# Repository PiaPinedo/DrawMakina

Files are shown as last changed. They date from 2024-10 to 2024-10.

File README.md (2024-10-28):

# DrawMakina
Máquina de dibujo Open Source 



DrawMakina es una maquina de dibujo DIY, Open Source y de bajo coste para dibujar con hojas tamaño A2.

Fabricada con perfiles V-slot , piezas impresas en 3d y carcasa cortada con laser cnc.

En este repositorio podrás acceder a la lista de piezas, el detalle del ensamblaje y las piezas para imprimir 3d.
DM completa
## Table of Contents
- [Listado Componentes](#listado-componentes)
- [Piezas STL-Para impresión 3D](#piezas-stl-para-impresión-3d)
- [Planos Ensamblaje](#planos-ensamblaje)
  - [Planos piezas con insertos](#planos-piezas-con-insertos)
  - [Planos Carro](#planos-carro)
  - [Planos Eje X](#planos-eje-x)
  - [Planos Eje Y+Base](#planos-eje-ybase)
  - [Planos Caja Electrónica](#planos-caja-electrónica)
  - [Planos Ensamble DrawMakina](#planos-ensamble-drawmakina)
- [Instagram](#instagram)

### [Listado Componentes](https://docs.google.com/spreadsheets/d/1AmNRzkBurb7ddMvps6KCj8CBwCPvgpXAdZpDU2fsMKk/edit?usp=sharing "Listado Componentes")

### [Piezas STL-Para impresión 3D](https://github.com/PiaPinedo/DrawMakina/tree/main/STL%20DrawMakina "Piezas STL-Para impresión 3D")

### [Planos Ensamblaje](https://github.com/PiaPinedo/DrawMakina/tree/main/Planos%20Ensamble%20DrawMakina "Planos Ensamblaje")

#### [Planos piezas con insertos](https://github.com/PiaPinedo/DrawMakina/blob/main/Planos%20Ensamble%20DrawMakina/00%20Planos%20Ensamble%20DrawMakina-Piezas%20impresas%20%5Bcon_insertos%5D.pdf "Planos piezas con insertos")

#### [Planos Carro](https://github.com/PiaPinedo/DrawMakina/blob/main/Planos%20Ensamble%20DrawMakina/01%20Planos%20Ensamble%20DrawMakina-%20CARRO.pdf "Planos carro")

#### [Planos Eje X](https://github.com/PiaPinedo/DrawMakina/blob/main/Planos%20Ensamble%20DrawMakina/02%20Planos%20Ensamble%20DrawMakina-EJE_X.pdf "Planos EJE_X")

#### [Planos Eje Y+Base](https://github.com/PiaPinedo/DrawMakina/blob/main/Planos%20Ensamble%20DrawMakina/03%20Planos%20Ensamble%20DrawMakina-EJE_Y-BASE.pdf "Planos EJE_Y+BASE")

#### [Planos Caja Electrónica](https://github.com/PiaPinedo/DrawMakina/blob/main/Planos%20Ensamble%20DrawMakina/04%20Planos%20Ensamble%20DrawMakina-Caja%20Electronica%20%5Bcon_espaciadores%5D.pdf "Planos CAJA ELECTRÓNICA")

#### [Planos Ensamble DrawMakina](https://github.com/PiaPinedo/DrawMakina/blob/main/Planos%20Ensamble%20DrawMakina/05%20Planos%20Ensamble%20DrawMakina.pdf "Planos Ensamble DrawMakina")

-------------

### [Instagram](https://www.instagram.com/drawmakina/)
Visita el instagram de DrawMakina para novedades.

0f

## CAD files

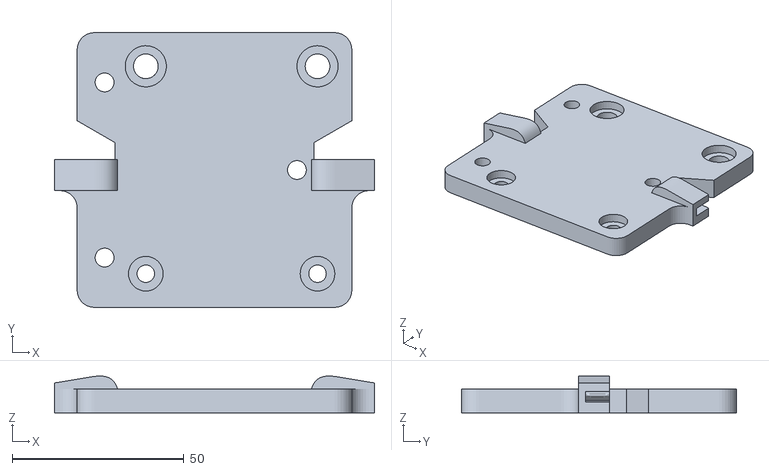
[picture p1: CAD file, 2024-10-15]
STL DrawMakina/CARRO_XY/Placa Carro Y.stl
93.2 x 80.0 x 10.8

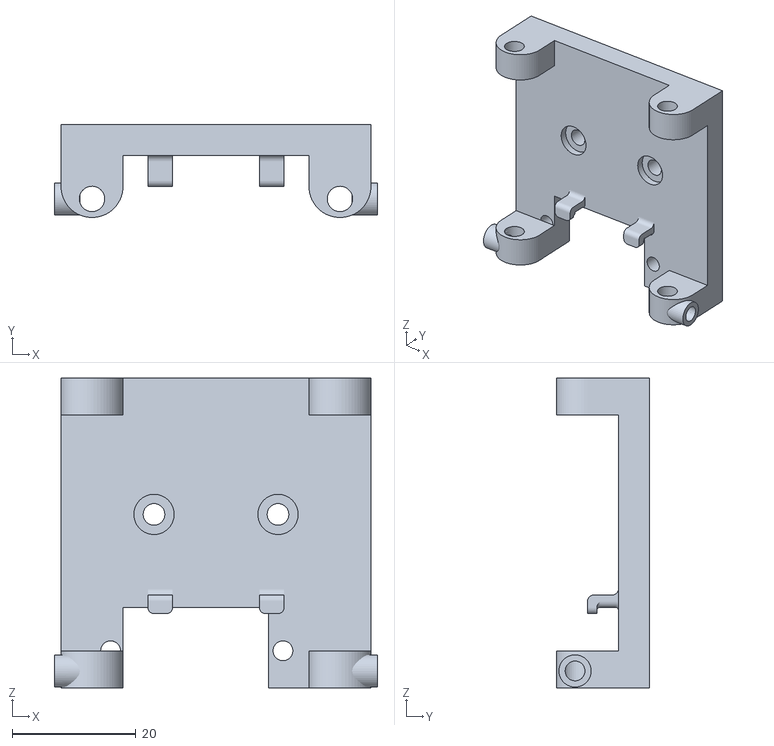
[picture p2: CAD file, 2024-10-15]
STL DrawMakina/EJE_X/Porta lapiz_2.stl
52.1 x 15.0 x 50.0

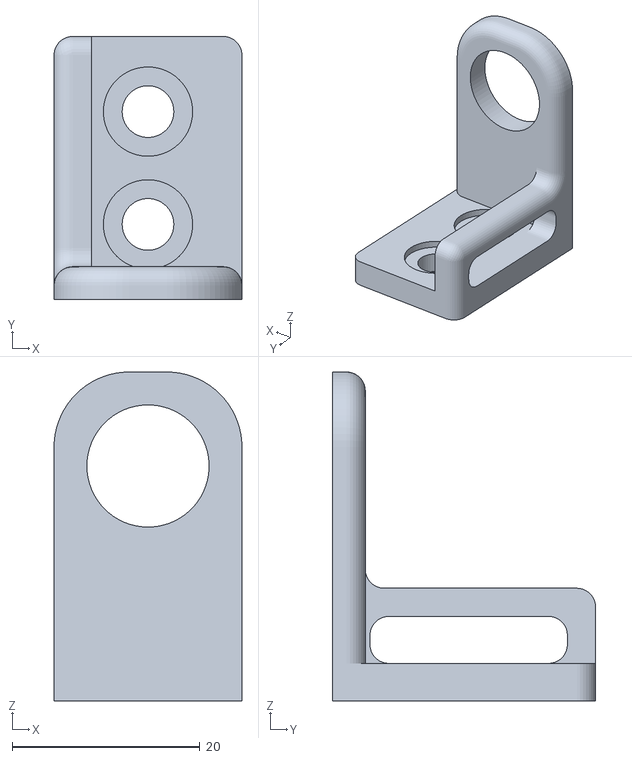
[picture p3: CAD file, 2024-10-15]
STL DrawMakina/EJE_Y + BASE/Pieza portacable_3.stl
20.0 x 28.0 x 35.0

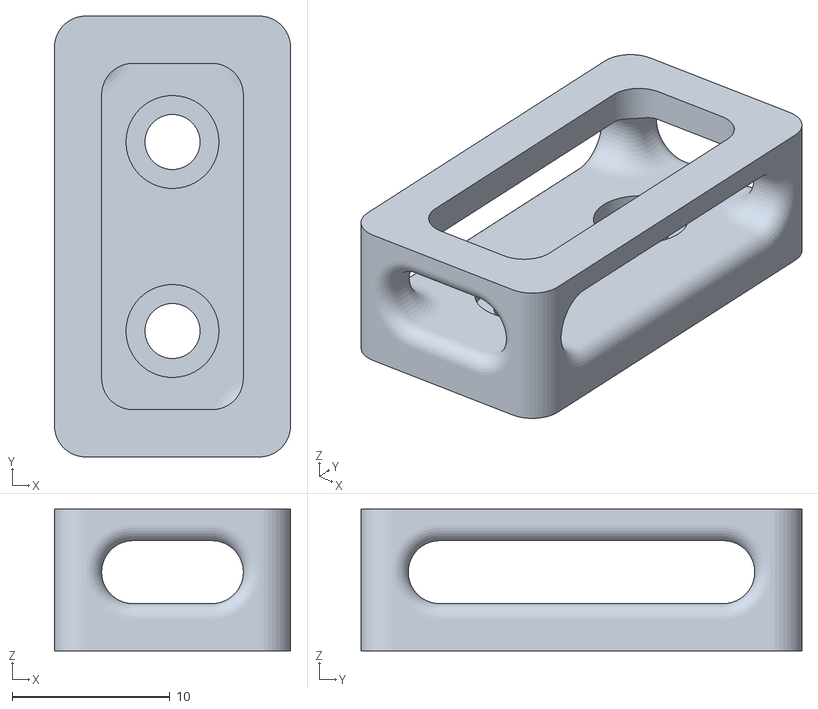
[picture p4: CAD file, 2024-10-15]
STL DrawMakina/CARRO_XY/Pieza Portacable_1.stl
15.0 x 28.0 x 9.00

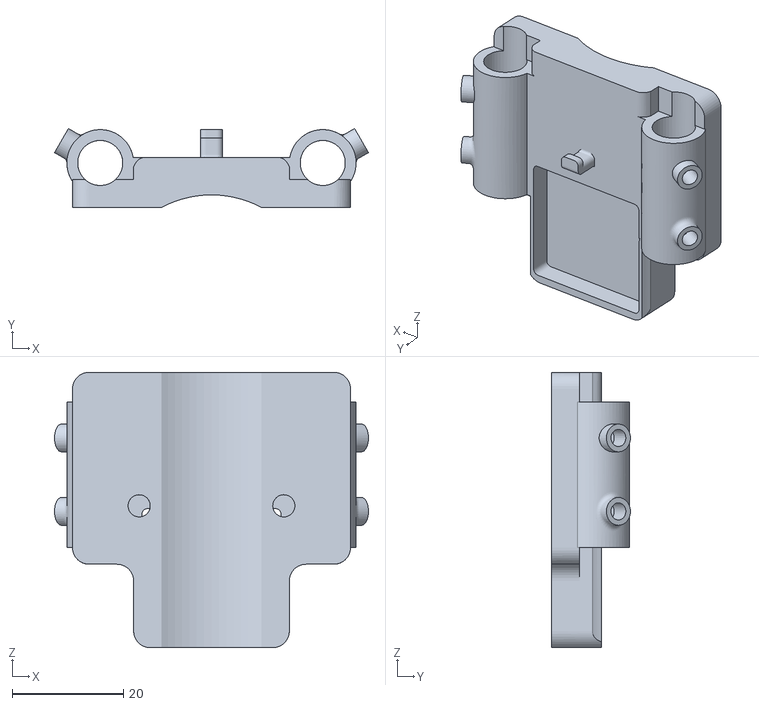
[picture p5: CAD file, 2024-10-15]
STL DrawMakina/EJE_X/Porta lapiz_3.stl
56.4 x 14.2 x 49.5

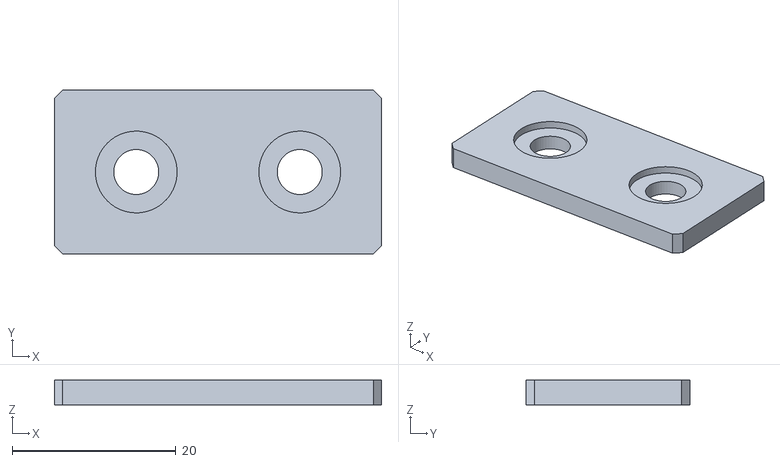
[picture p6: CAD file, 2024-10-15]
STL DrawMakina/EJE_Y + BASE/Tapa 20x40.stl
40.0 x 20.0 x 3.00

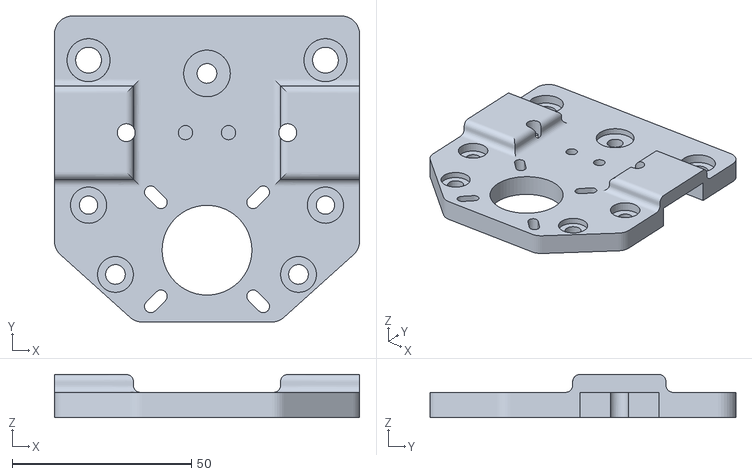
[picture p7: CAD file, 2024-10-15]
STL DrawMakina/CARRO_XY/Placa Carro X.stl
85.0 x 85.2 x 12.0

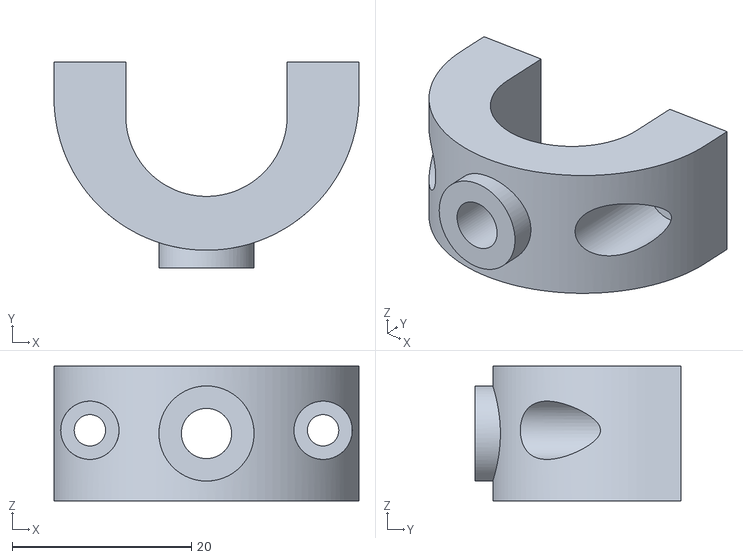
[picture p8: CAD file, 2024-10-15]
STL DrawMakina/EJE_X/Porta lapiz_4.stl
34.0 x 23.0 x 15.0

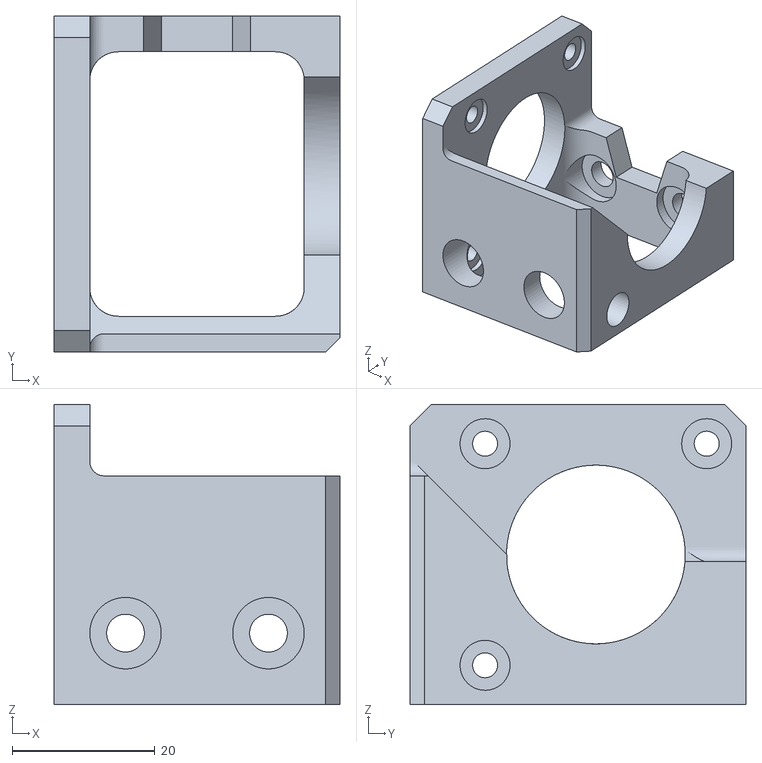
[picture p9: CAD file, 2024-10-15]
STL DrawMakina/EJE_Y + BASE/Pieza Motor_Y.stl
40.0 x 47.0 x 42.0

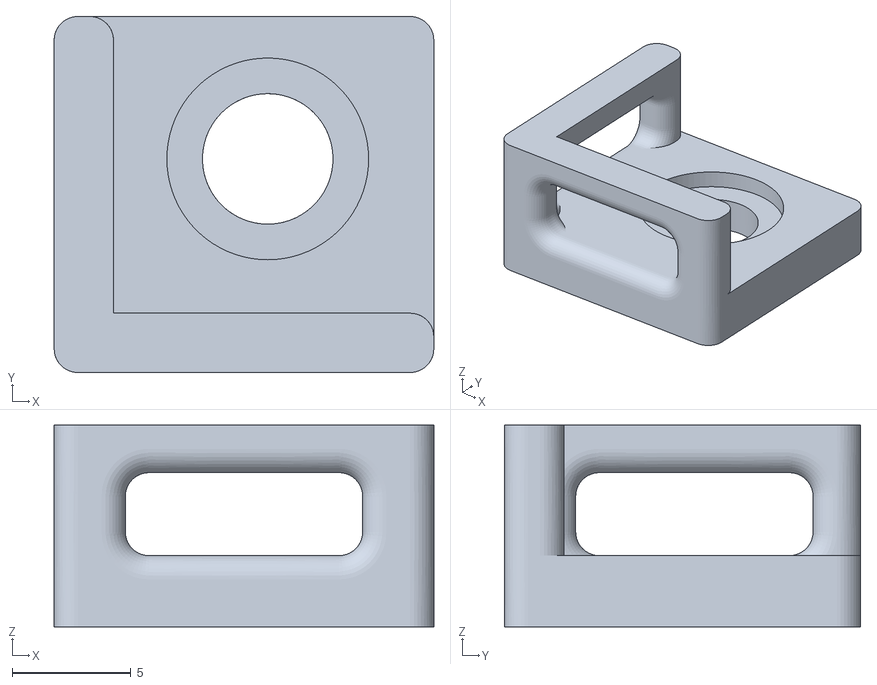
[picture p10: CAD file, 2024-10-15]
STL DrawMakina/EJE_X/Pieza portacable_2.stl
16.0 x 15.0 x 8.50

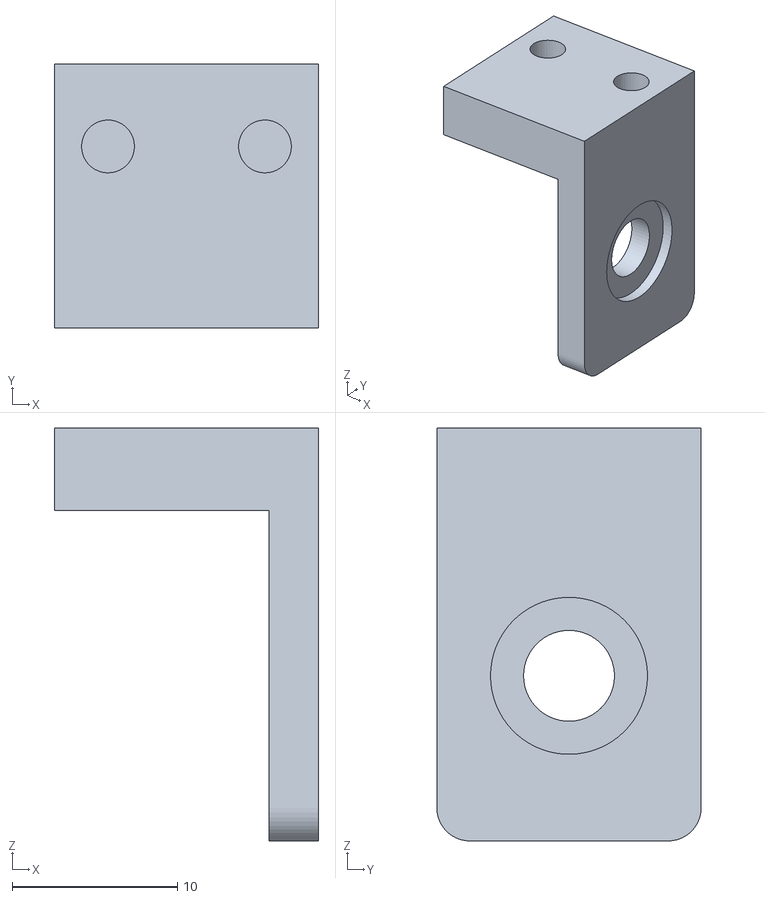
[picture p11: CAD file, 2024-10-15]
STL DrawMakina/EJE_Y + BASE/Pieza final carrera.stl
16.0 x 16.0 x 25.0

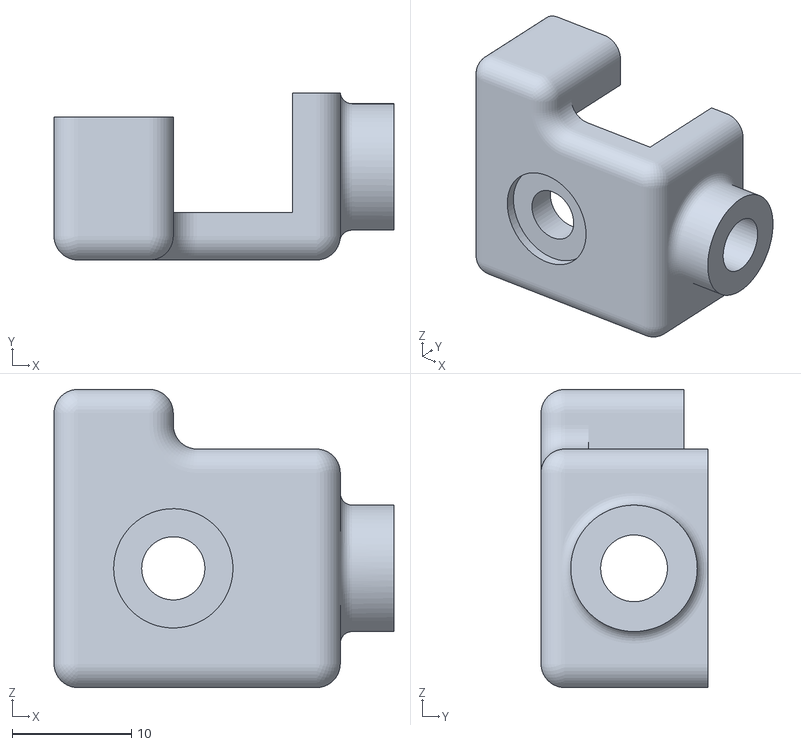
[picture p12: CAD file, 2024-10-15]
STL DrawMakina/EJE_X/Pieza Final X v2.stl
28.5 x 14.0 x 25.0

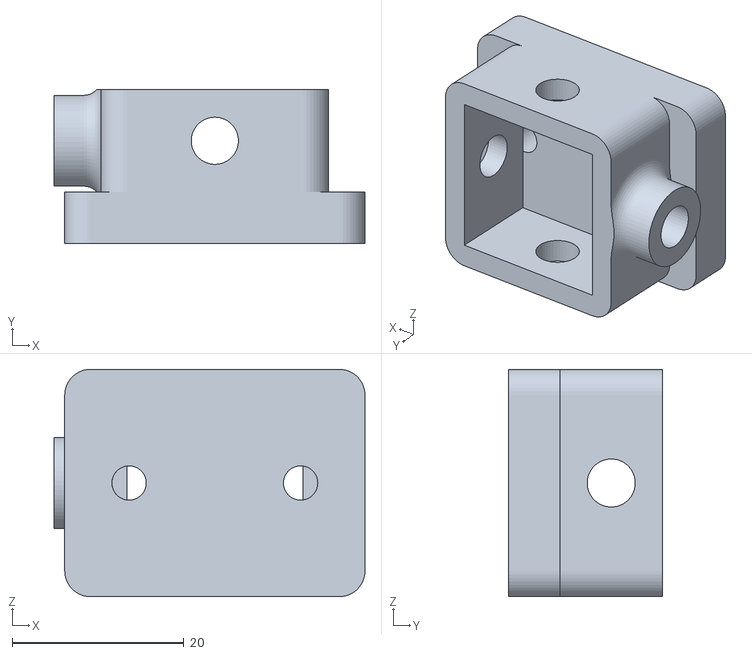
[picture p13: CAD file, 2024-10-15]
STL DrawMakina/EJE_X/Porta lapiz_1.stl
36.2 x 18.0 x 26.5

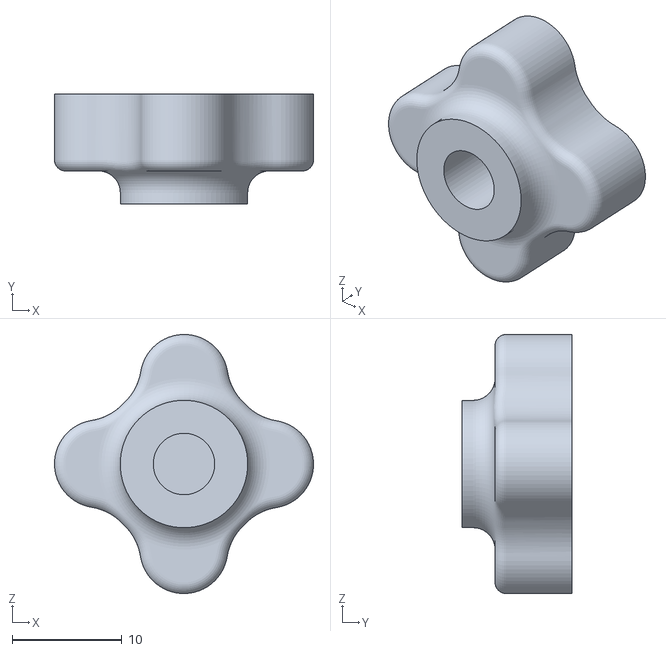
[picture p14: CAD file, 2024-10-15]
STL DrawMakina/EJE_X/Porta lapiz_Roseta.stl
23.6 x 10.0 x 23.6

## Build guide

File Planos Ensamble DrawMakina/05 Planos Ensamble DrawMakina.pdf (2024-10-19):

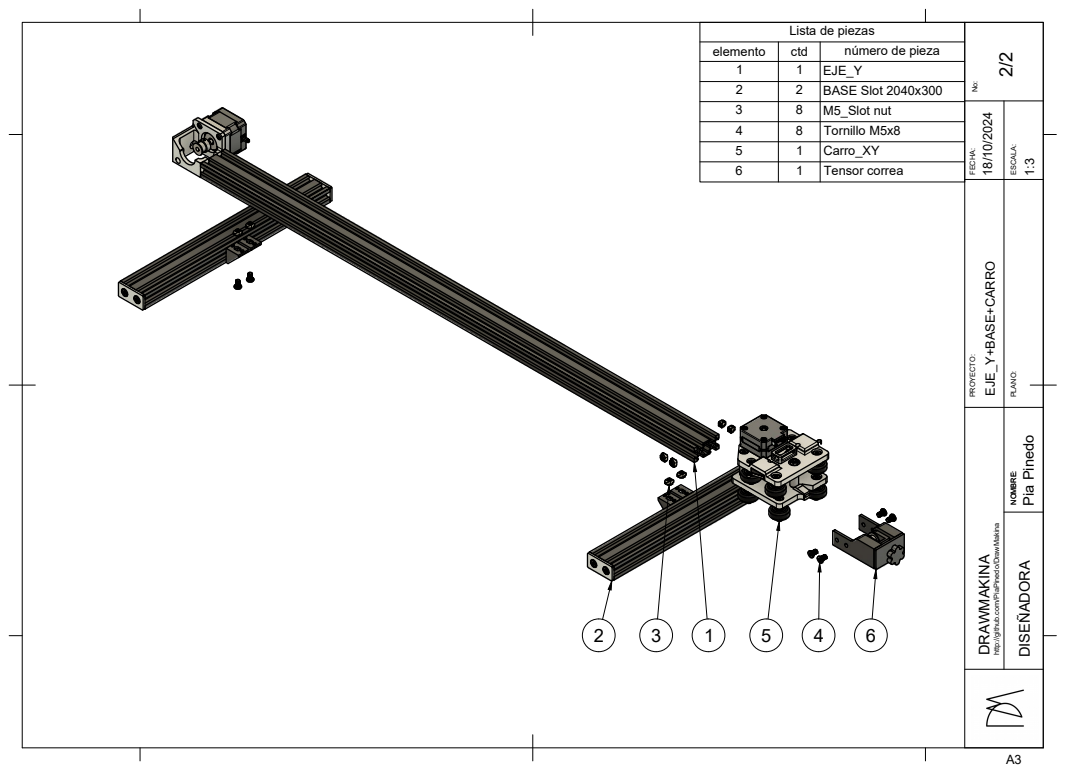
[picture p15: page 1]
DRAWMAKINA; DISEÑADORA; NOMBRE: PLANO:; PROYECTO:; NOMBRE: ESCALA:; FECHA: No:; Pia Pinedo; elemento; ctd; número de pieza; EJE_Y; BASE Slot 2040x300; M5_Slot nut 4; Tornillo M5x8; Carro_XY; Tensor correa

Lista de piezas

http://github.com/PiaPinedo/DrawMakina EJE_Y+BASE+CARRO 18/10/2024

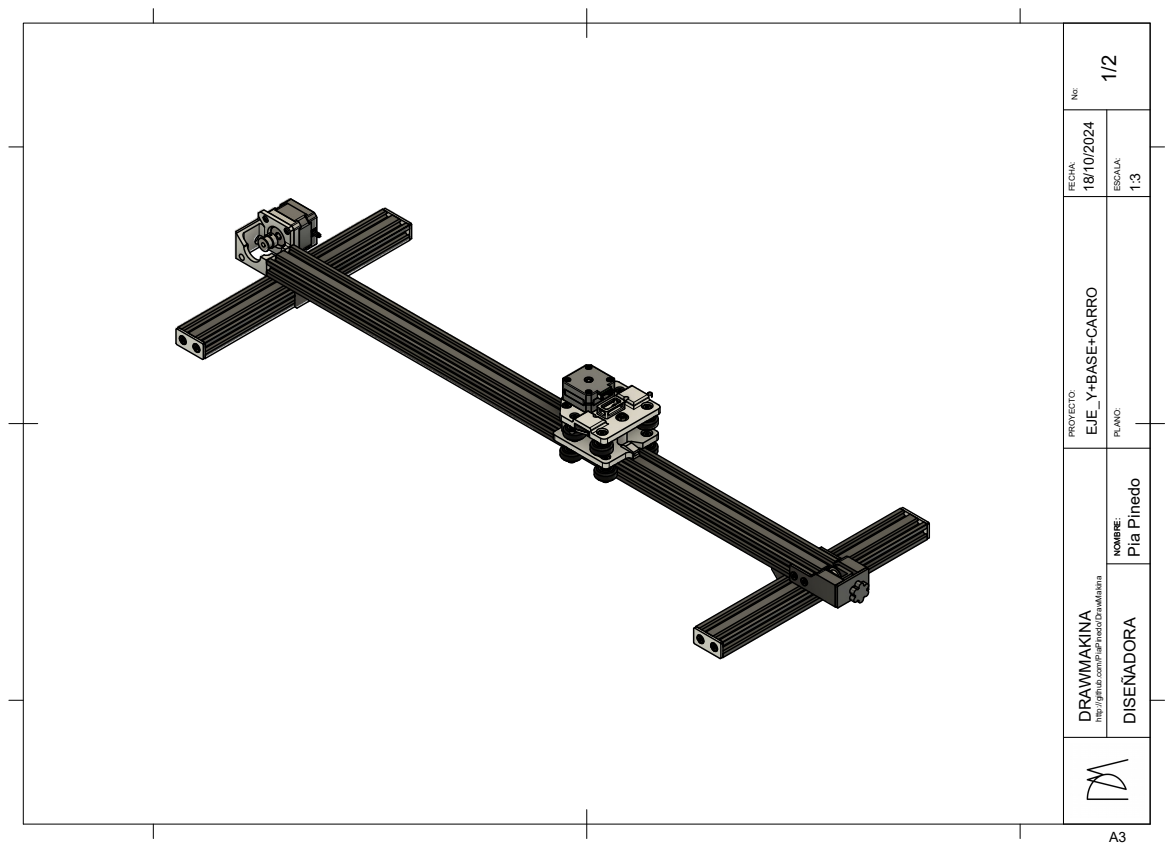
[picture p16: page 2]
DRAWMAKINA; DISEÑADORA; NOMBRE: PLANO:; PROYECTO:; NOMBRE: ESCALA:; FECHA: No:; Pia Pinedo

http://github.com/PiaPinedo/DrawMakina EJE_Y+BASE+CARRO 18/10/2024

1

2

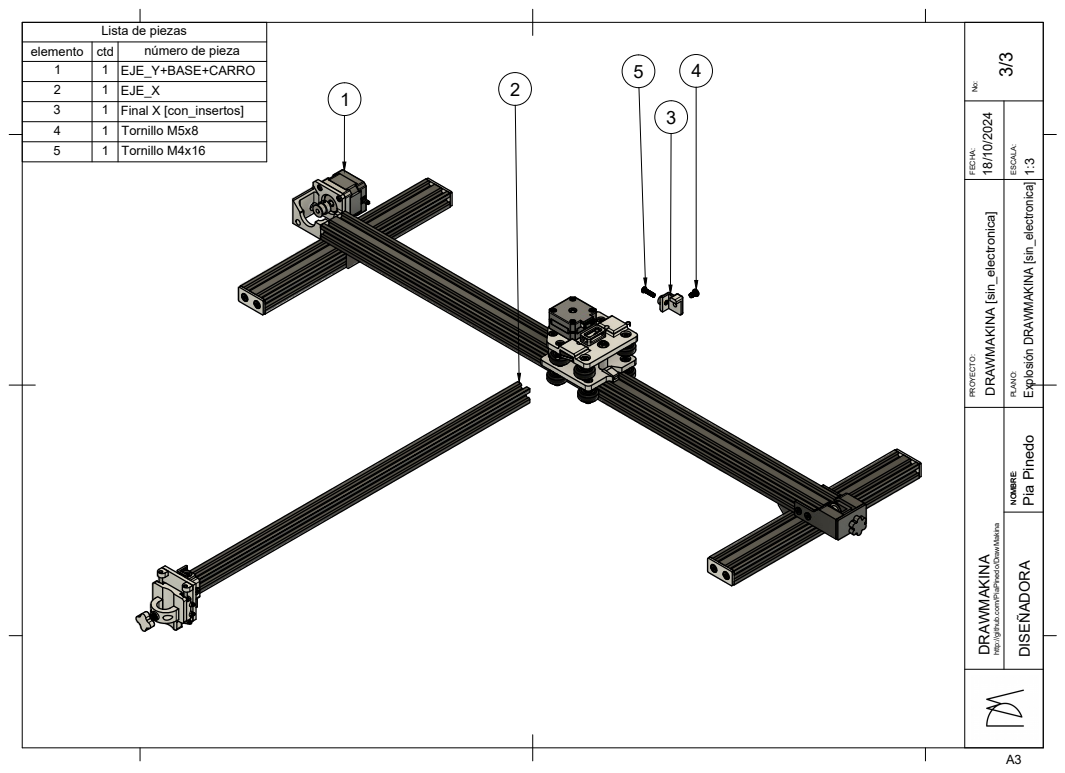
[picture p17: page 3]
DRAWMAKINA; DISEÑADORA; NOMBRE: PLANO:; PROYECTO:; NOMBRE: ESCALA:; FECHA: No:; Pia Pinedo; Explosión DRAWMAKINA [sin_electronica]; elemento; ctd; número de pieza; EJE_Y+BASE+CARRO; EJE_X; Final X [con_insertos] 4; Tornillo M5x8; Tornillo M4x16

Lista de piezas

http://github.com/PiaPinedo/DrawMakina DRAWMAKINA [sin_electronica]

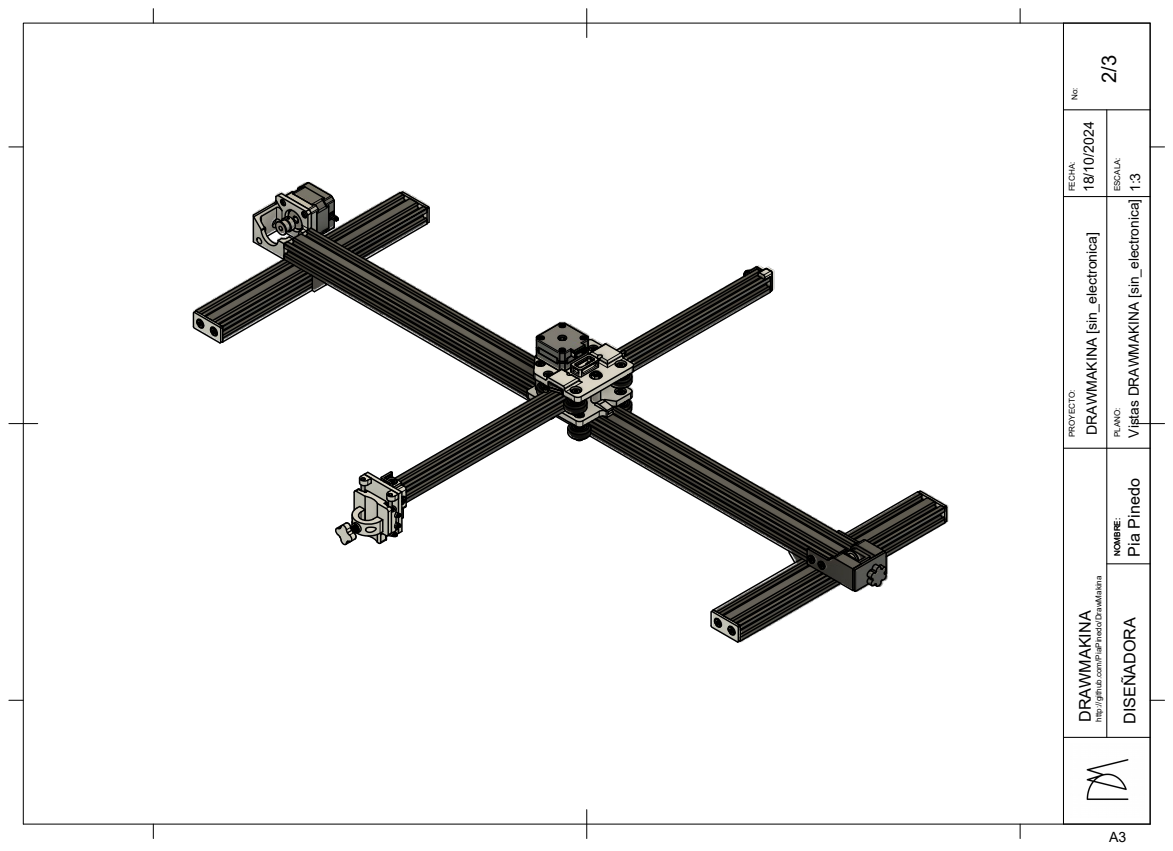
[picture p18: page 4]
DRAWMAKINA; DISEÑADORA; NOMBRE: PLANO:; PROYECTO:; NOMBRE: ESCALA:; FECHA: No:; Pia Pinedo; Vistas DRAWMAKINA [sin_electronica]

http://github.com/PiaPinedo/DrawMakina DRAWMAKINA [sin_electronica]

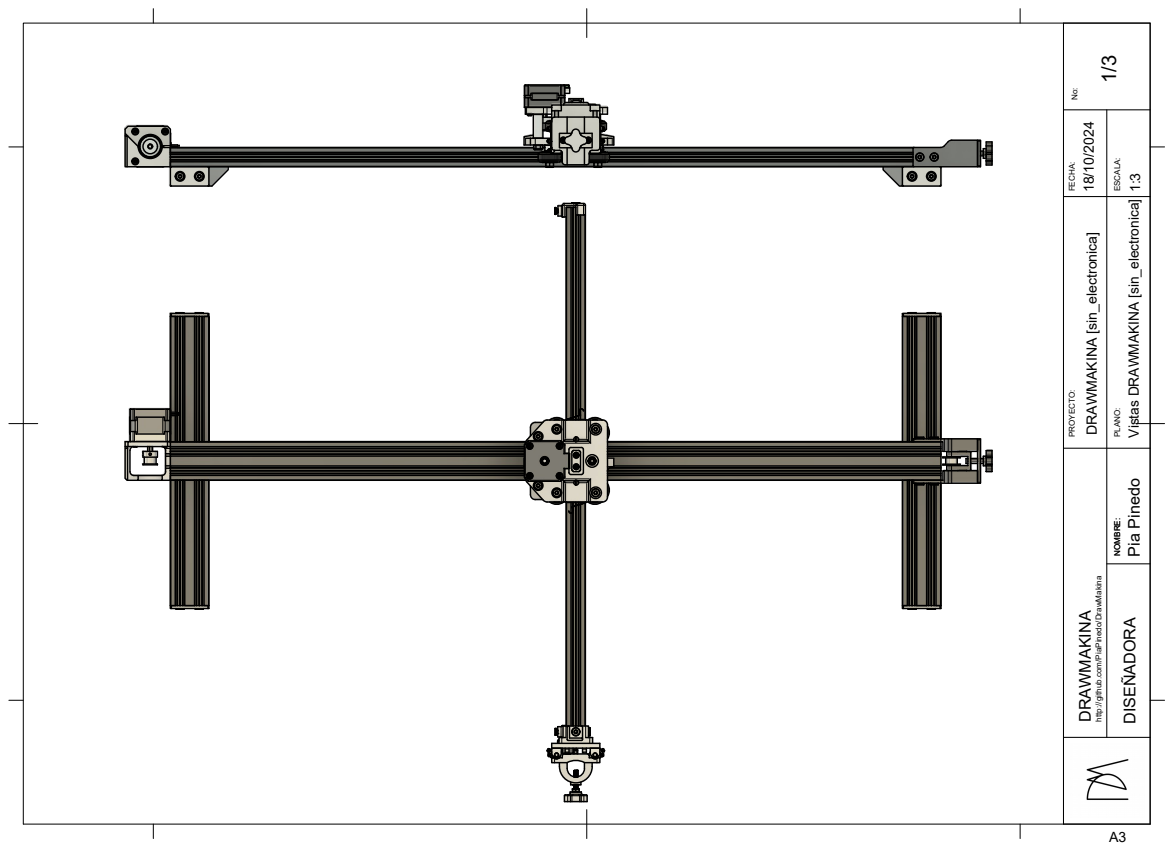
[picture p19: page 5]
DRAWMAKINA; DISEÑADORA; NOMBRE: PLANO:; PROYECTO:; NOMBRE: ESCALA:; FECHA: No:; Pia Pinedo; Vistas DRAWMAKINA [sin_electronica]

http://github.com/PiaPinedo/DrawMakina DRAWMAKINA [sin_electronica]

11

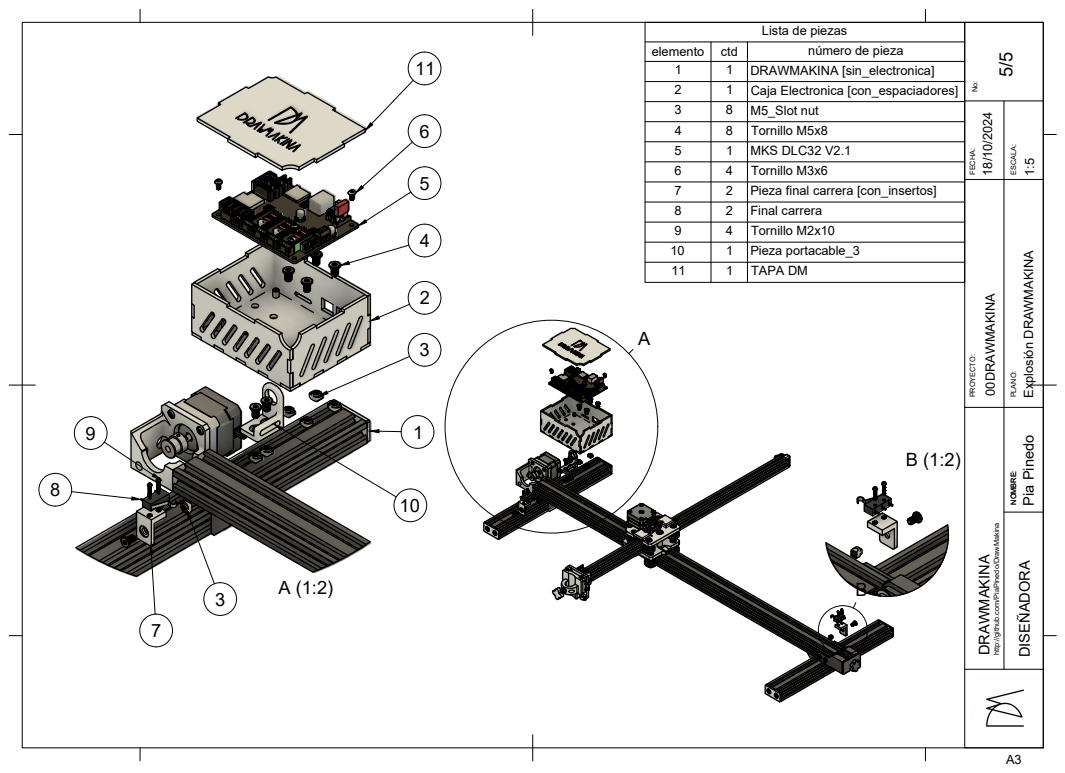
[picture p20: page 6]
DRAWMAKINA; DISEÑADORA; NOMBRE: PLANO:; PROYECTO:; NOMBRE: ESCALA:; FECHA: No:; Pia Pinedo; Explosión DRAWMAKINA; elemento ctd; número de pieza; 1 1 DRAWMAKINA [sin_electronica] 2 1 Caja Electronica [con_espaciadores]; 8 M5_Slot nut 4; 8 Tornillo M5x8; 1 MKS DLC32 V2.1 6; 4 Tornillo M3x6 7; 2 Pieza final carrera [con_insertos]; 2 Final carrera 9; 4 Tornillo M2x10; 10 1 Pieza portacable_3 11 1 TAPA DM

Lista de piezas

http://github.com/PiaPinedo/DrawMakina 00DRAWMAKINA

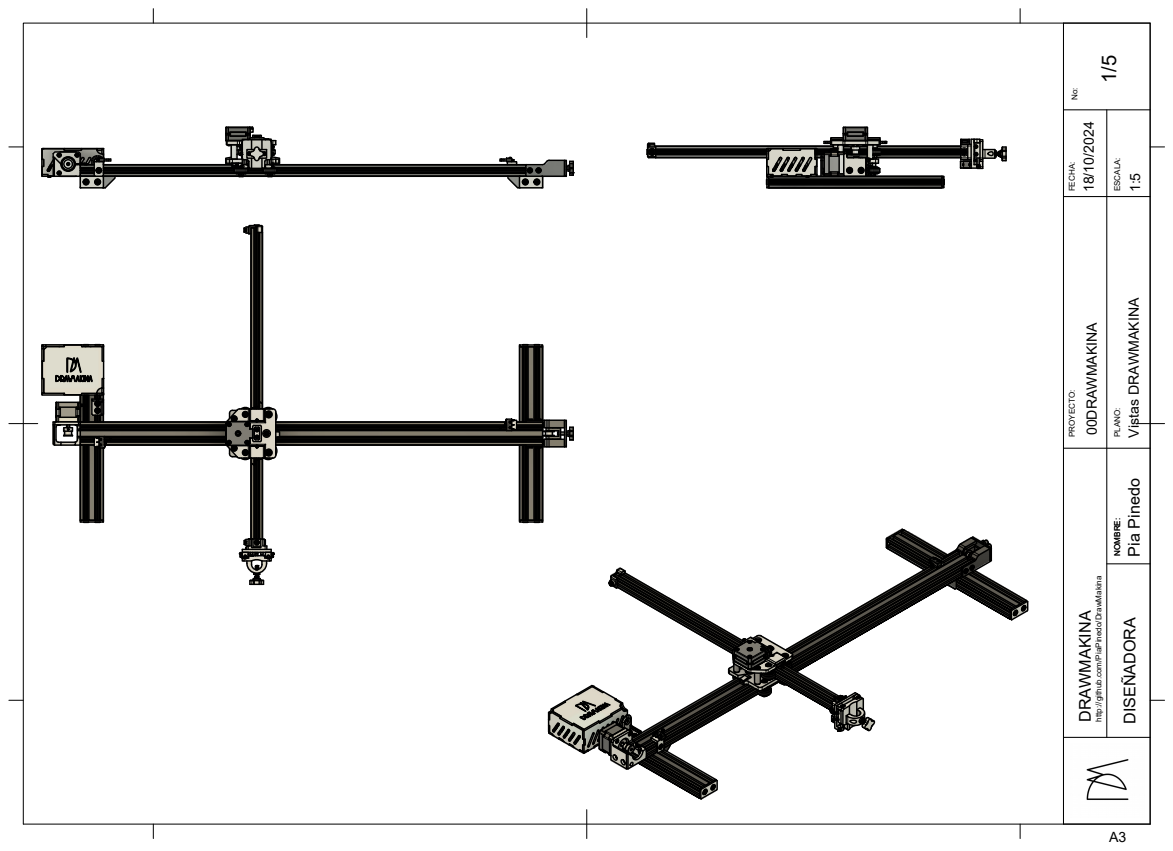
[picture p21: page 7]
DRAWMAKINA; DISEÑADORA; NOMBRE: PLANO:; PROYECTO:; NOMBRE: ESCALA:; FECHA: No:; Pia Pinedo; Vistas DRAWMAKINA

http://github.com/PiaPinedo/DrawMakina 00DRAWMAKINA

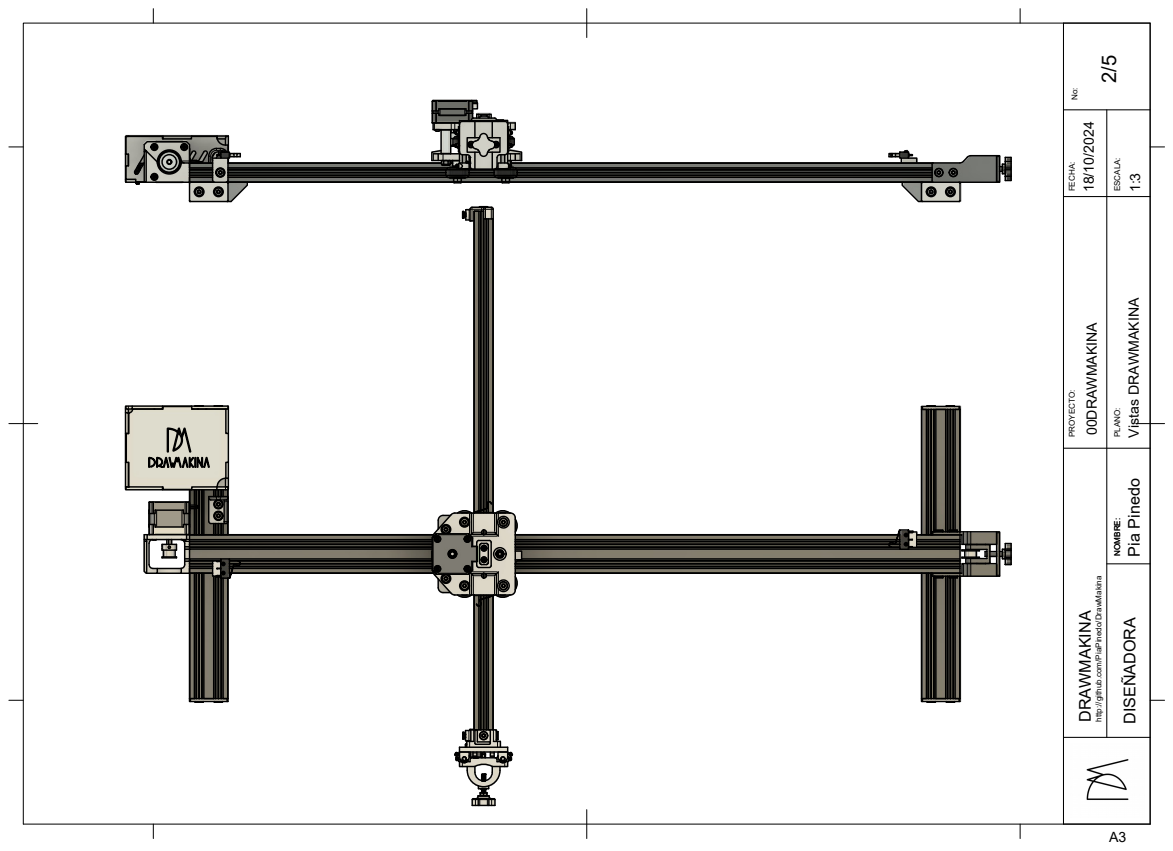
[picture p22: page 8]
DRAWMAKINA; DISEÑADORA; NOMBRE: PLANO:; PROYECTO:; NOMBRE: ESCALA:; FECHA: No:; Pia Pinedo; Vistas DRAWMAKINA

http://github.com/PiaPinedo/DrawMakina 00DRAWMAKINA

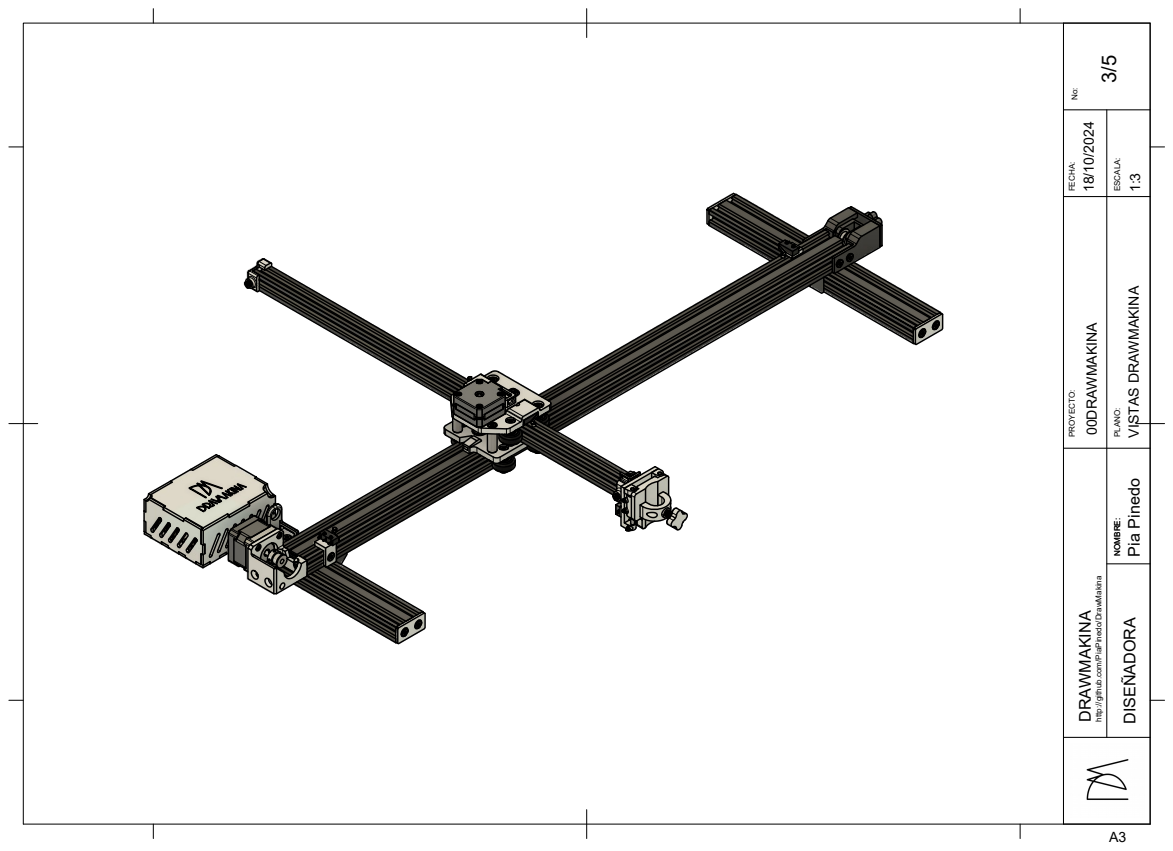
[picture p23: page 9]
DRAWMAKINA; DISEÑADORA; NOMBRE: PLANO:; PROYECTO:; NOMBRE: ESCALA:; FECHA: No:; Pia Pinedo; VISTAS DRAWMAKINA

http://github.com/PiaPinedo/DrawMakina 00DRAWMAKINA

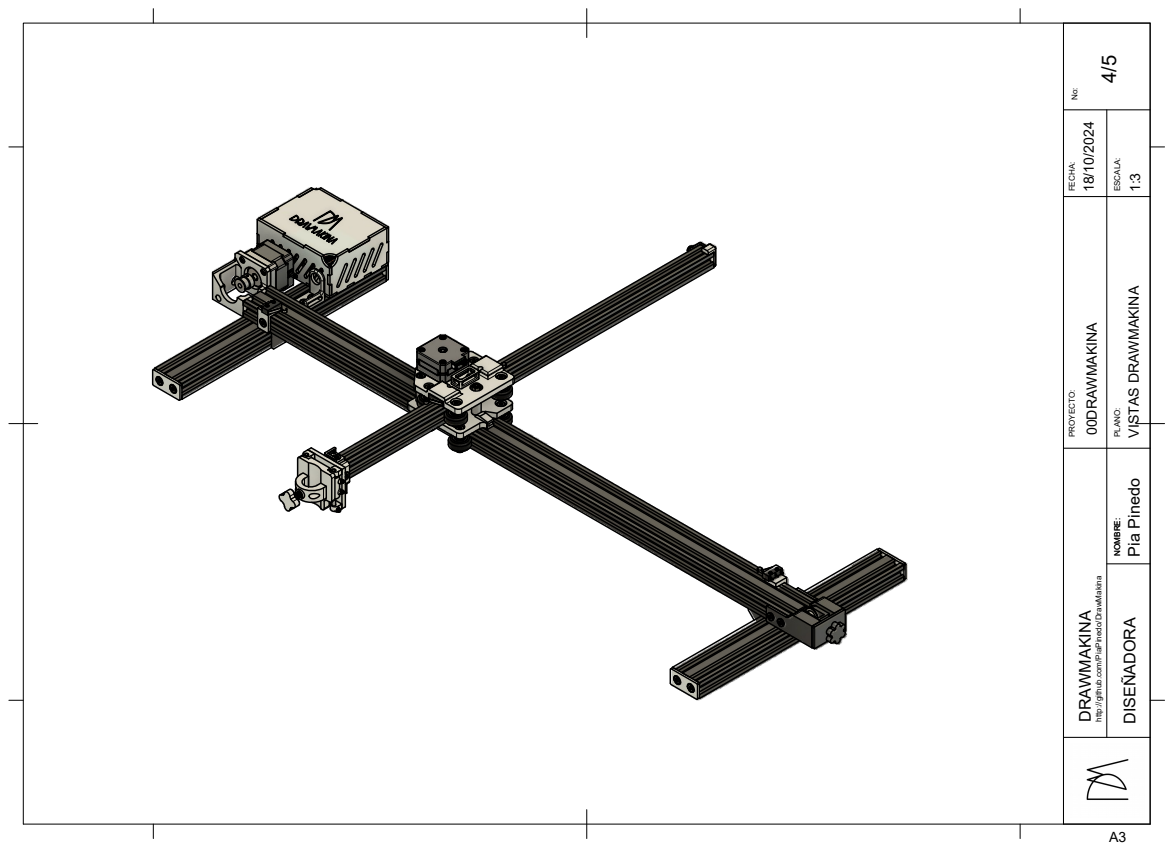
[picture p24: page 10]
DRAWMAKINA; DISEÑADORA; NOMBRE: PLANO:; PROYECTO:; NOMBRE: ESCALA:; FECHA: No:; Pia Pinedo; VISTAS DRAWMAKINA

http://github.com/PiaPinedo/DrawMakina 00DRAWMAKINA

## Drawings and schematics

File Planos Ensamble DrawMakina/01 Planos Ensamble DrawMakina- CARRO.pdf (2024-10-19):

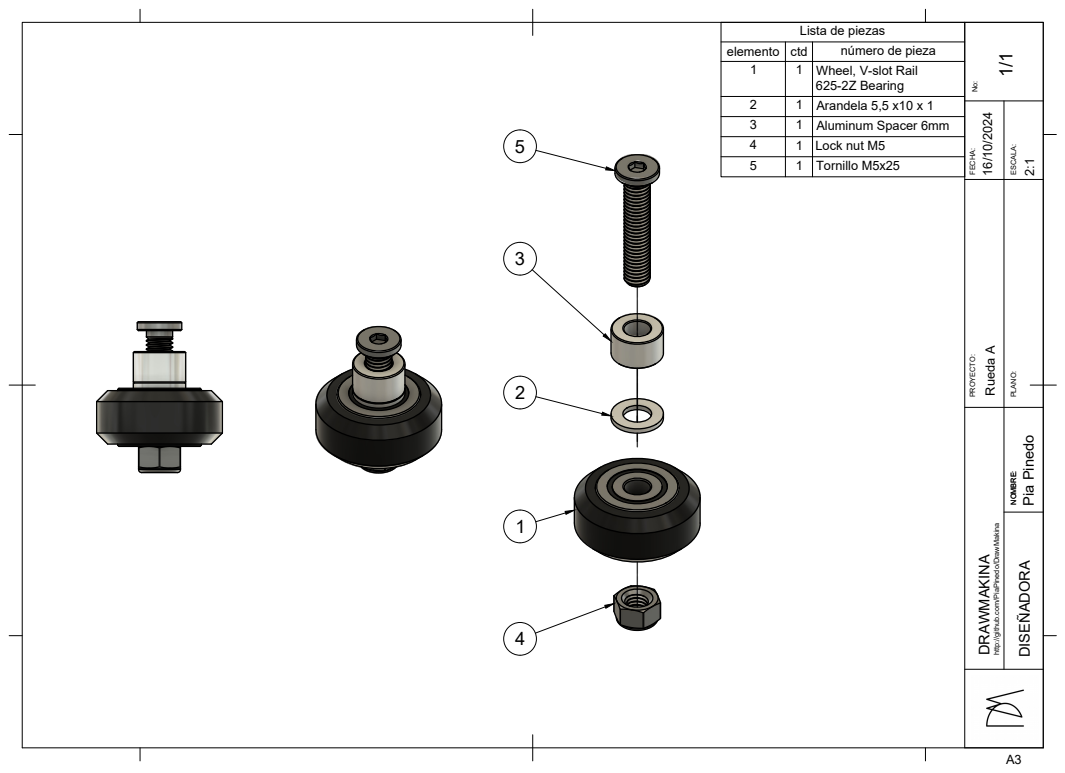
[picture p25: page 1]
DRAWMAKINA; DISEÑADORA; NOMBRE: PLANO:; PROYECTO:; NOMBRE: ESCALA:; FECHA: No:; Pia Pinedo; elemento; ctd; número de pieza; Wheel, V-slot Rail; 625-2Z Bearing; Arandela 5,5 x10 x 1; Aluminum Spacer 6mm 4; Lock nut M5 5; Tornillo M5x25

Lista de piezas

http://github.com/PiaPinedo/DrawMakina Rueda A 16/10/2024

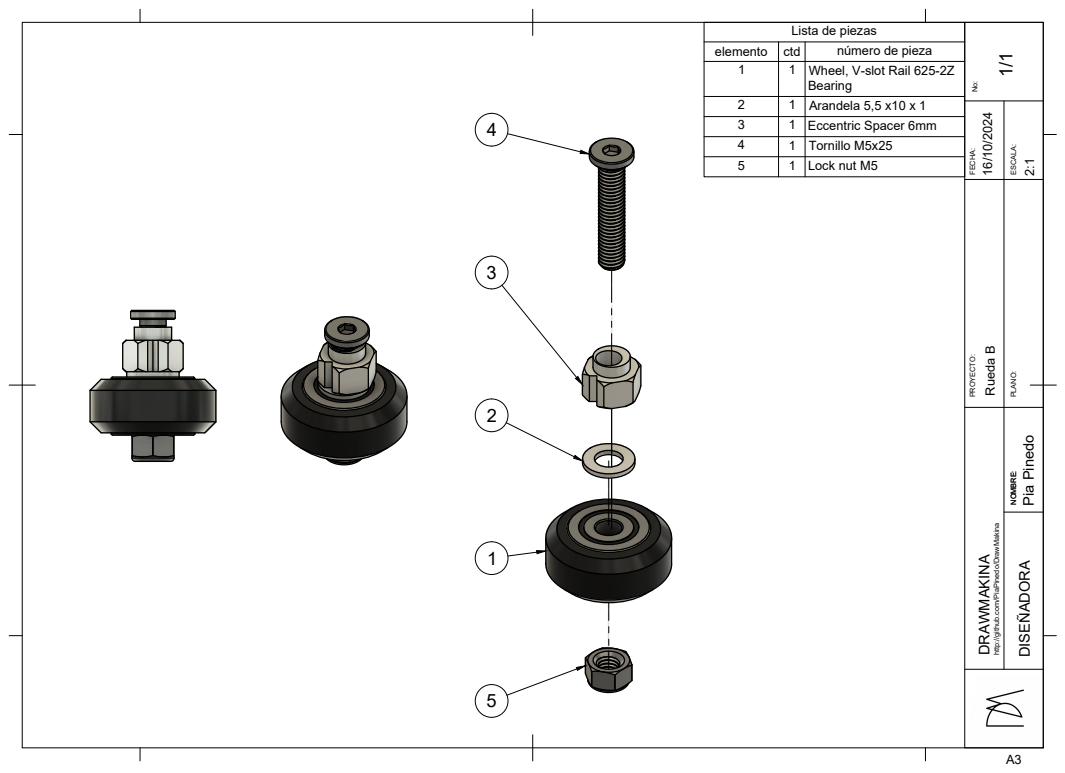
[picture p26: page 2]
DRAWMAKINA; DISEÑADORA; NOMBRE: PLANO:; PROYECTO:; NOMBRE: ESCALA:; FECHA: No:; Pia Pinedo; elemento; ctd; número de pieza; Wheel, V-slot Rail 625-2Z; Bearing; Arandela 5,5 x10 x 1; Eccentric Spacer 6mm 4; Tornillo M5x25 5; Lock nut M5

http://github.com/PiaPinedo/DrawMakina Rueda B 16/10/2024

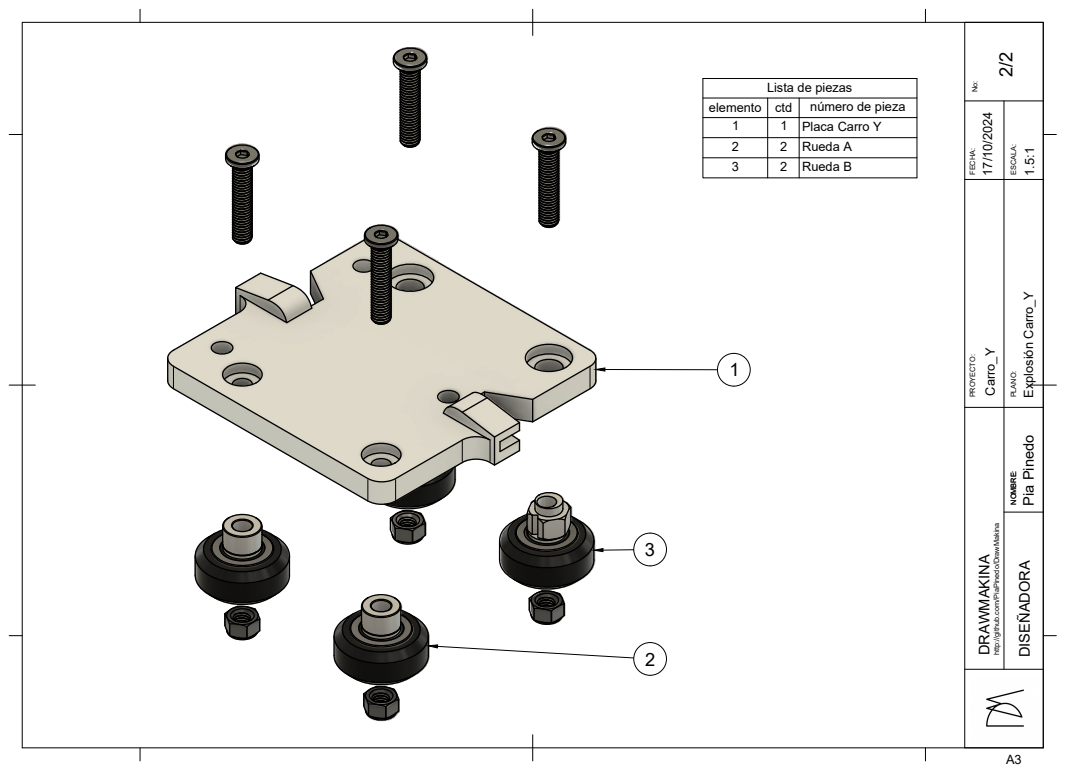
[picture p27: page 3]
DRAWMAKINA; DISEÑADORA; NOMBRE: PLANO:; PROYECTO:; NOMBRE: ESCALA:; FECHA: No:; Pia Pinedo; Explosión Carro_Y; elemento; ctd; número de pieza; Placa Carro Y; Rueda A; Rueda B

Lista de piezas

http://github.com/PiaPinedo/DrawMakina Carro_Y

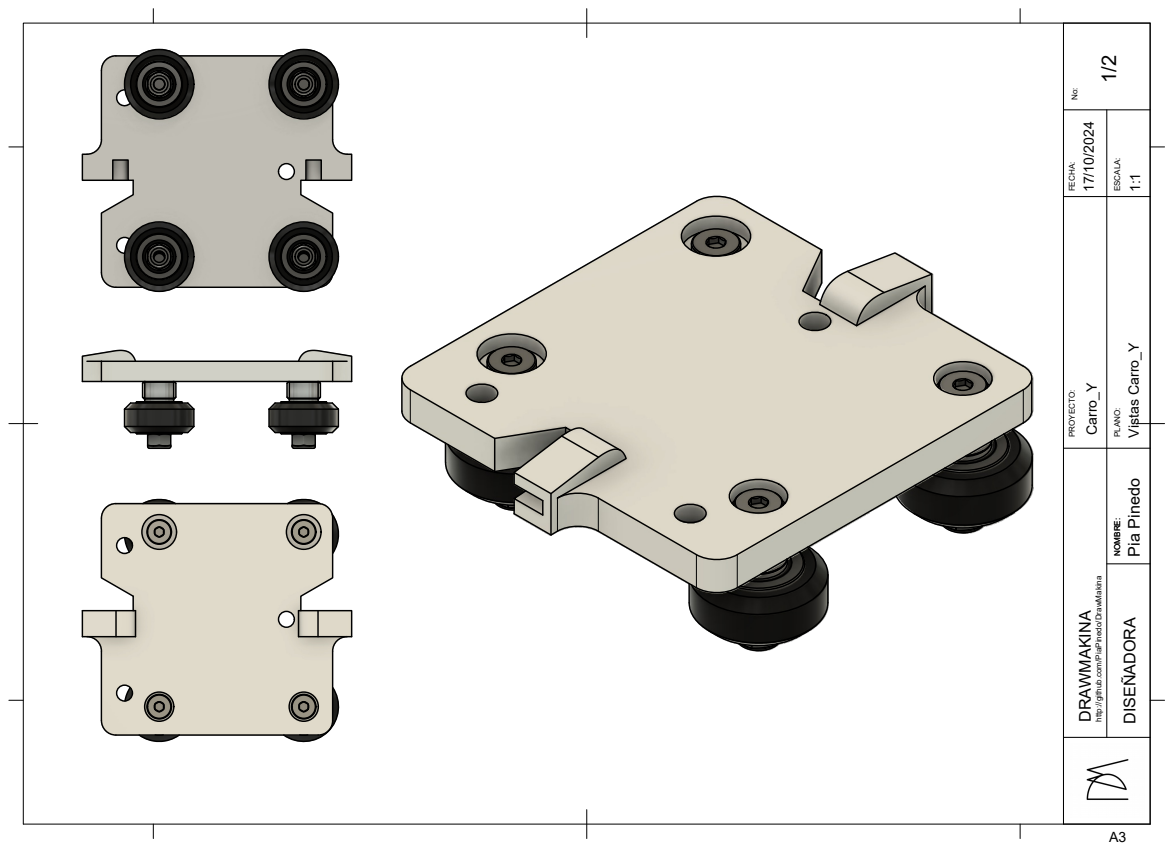
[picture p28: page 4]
DRAWMAKINA; DISEÑADORA; NOMBRE: PLANO:; PROYECTO:; NOMBRE: ESCALA:; FECHA: No:; Pia Pinedo; Vistas Carro_Y

http://github.com/PiaPinedo/DrawMakina Carro_Y

104

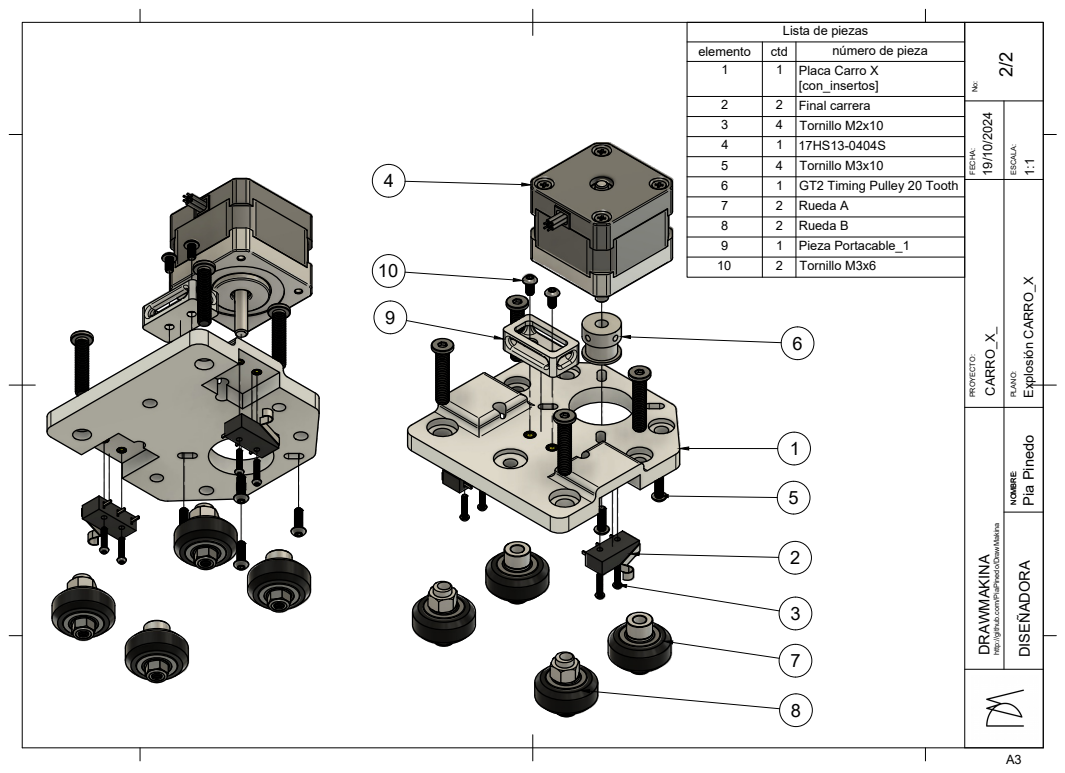
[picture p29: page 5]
DRAWMAKINA; DISEÑADORA; NOMBRE: PLANO:; PROYECTO:; NOMBRE: ESCALA:; FECHA: No:; Pia Pinedo; Explosión CARRO_X; elemento; ctd; número de pieza; Placa Carro X; [con_insertos]; Final carrera 3; Tornillo M2x10; Tornillo M3x10; GT2 Timing Pulley 20 Tooth 7; Rueda A; Rueda B; Pieza Portacable_1; Tornillo M3x6 873215

http://github.com/PiaPinedo/DrawMakina CARRO_X_

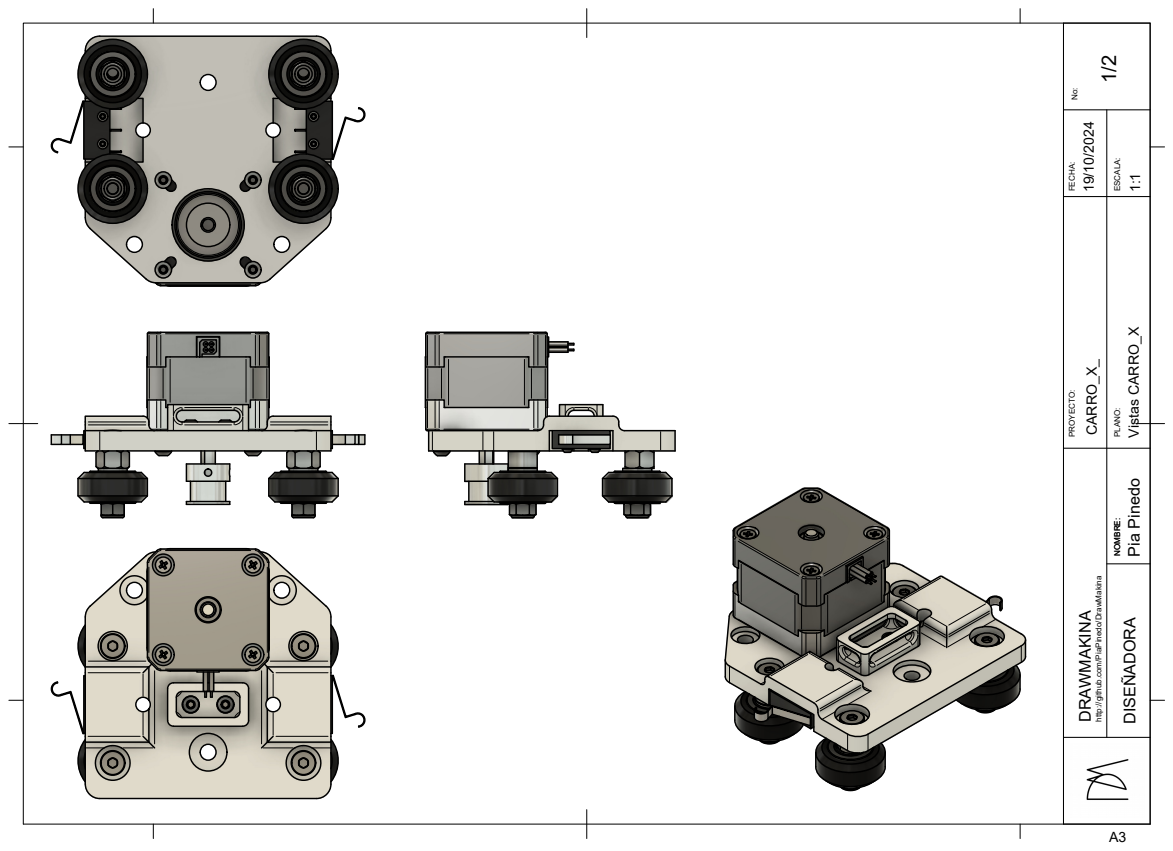
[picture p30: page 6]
DRAWMAKINA; DISEÑADORA; NOMBRE: PLANO:; PROYECTO:; NOMBRE: ESCALA:; FECHA: No:; Pia Pinedo; Vistas CARRO_X

http://github.com/PiaPinedo/DrawMakina CARRO_X_

4

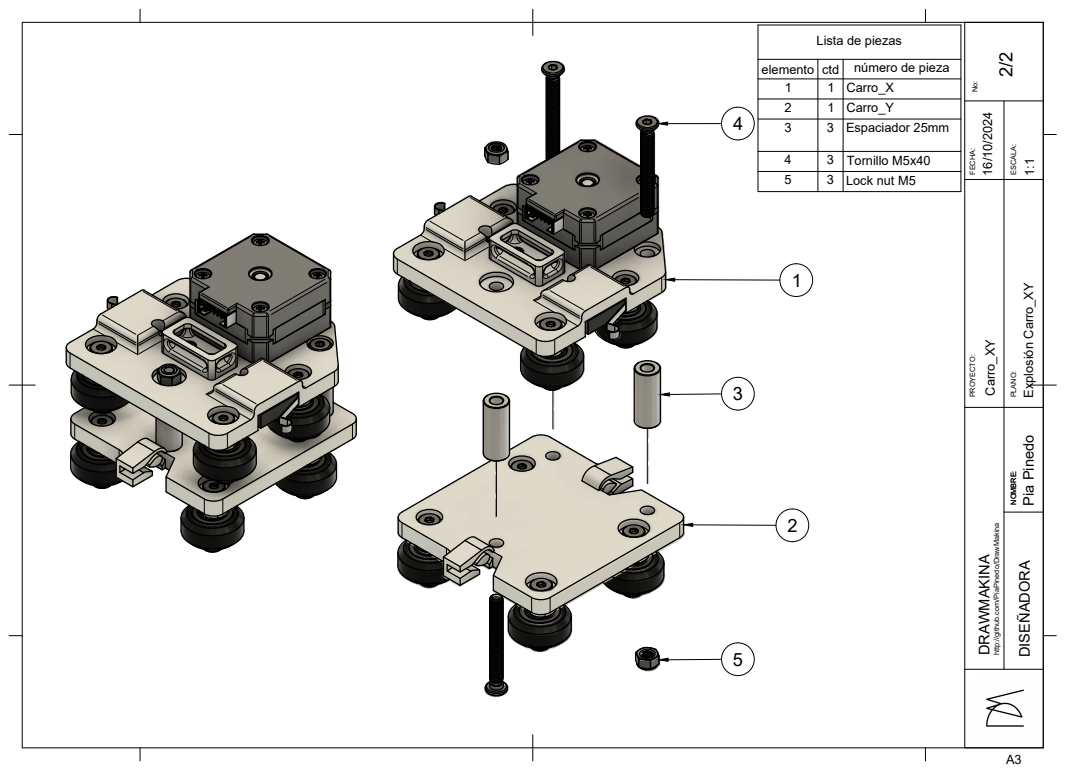
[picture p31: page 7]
DRAWMAKINA; DISEÑADORA; NOMBRE: PLANO:; PROYECTO:; NOMBRE: ESCALA:; FECHA: No:; Pia Pinedo; Explosión Carro_XY; elemento; ctd; número de pieza; Carro_X; Carro_Y; Espaciador 25mm; Tornillo M5x40; Lock nut M5

http://github.com/PiaPinedo/DrawMakina Carro_XY

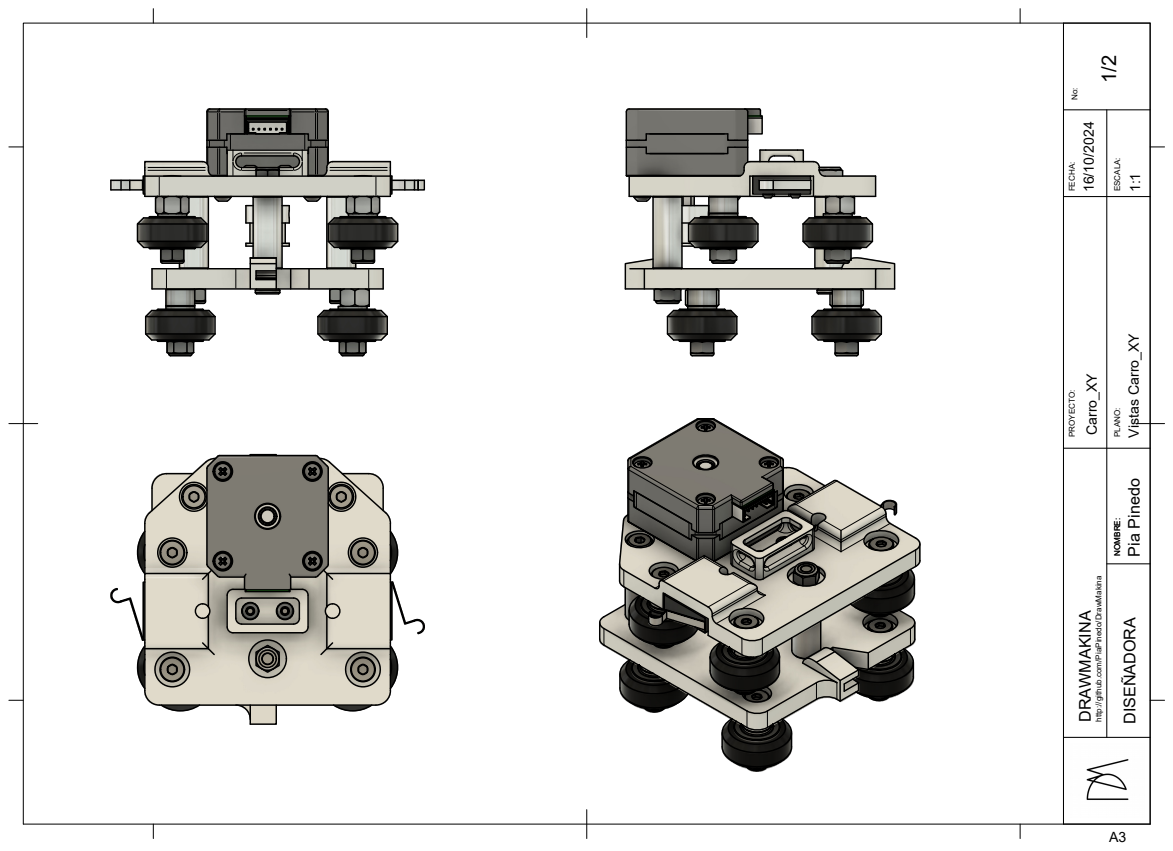
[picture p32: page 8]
DRAWMAKINA; DISEÑADORA; NOMBRE: PLANO:; PROYECTO:; NOMBRE: ESCALA:; FECHA: No:; Pia Pinedo; Vistas Carro_XY

http://github.com/PiaPinedo/DrawMakina Carro_XY

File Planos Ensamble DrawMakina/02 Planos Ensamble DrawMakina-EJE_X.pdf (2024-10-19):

106

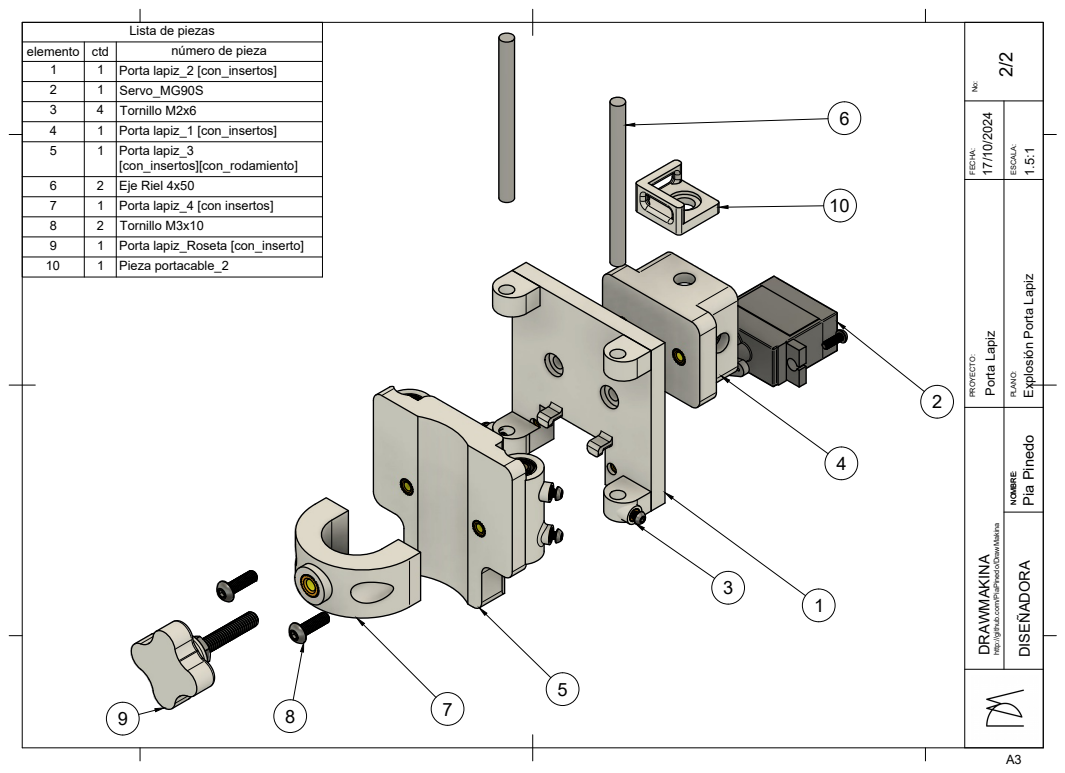
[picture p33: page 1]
DRAWMAKINA; DISEÑADORA; NOMBRE: PLANO:; PROYECTO:; NOMBRE: ESCALA:; FECHA: No:; Pia Pinedo; elemento; ctd; número de pieza; Porta lapiz_2 [con_insertos]; Servo_MG90S 3; Tornillo M2x6 4; Porta lapiz_1 [con_insertos]; Porta lapiz_3; [con_insertos][con_rodamiento]; Eje Riel 4x50 7; Porta lapiz_4 [con insertos]; Tornillo M3x10; Porta lapiz_Roseta [con_inserto]; Pieza portacable_2

Lista de piezas

Explosión Porta Lapiz

http://github.com/PiaPinedo/DrawMakina Porta Lapiz

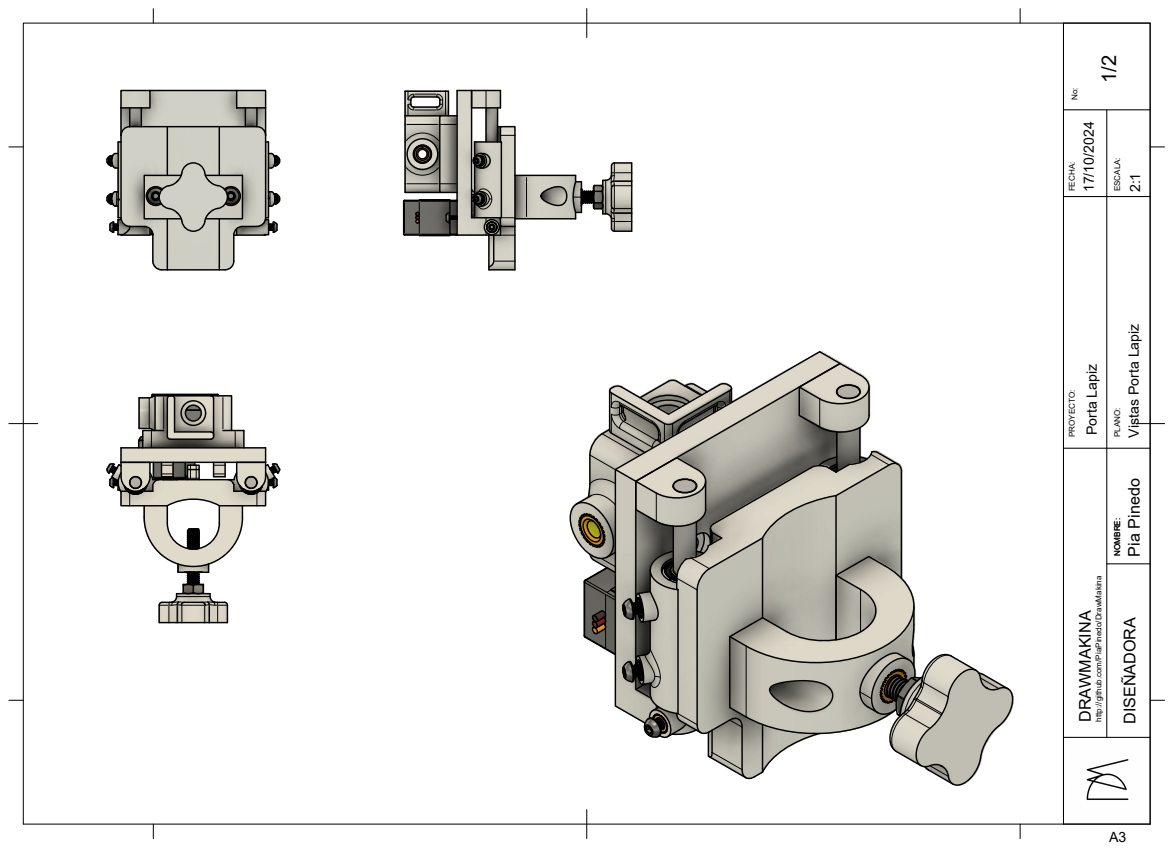
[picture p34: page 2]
DRAWMAKINA; DISEÑADORA; NOMBRE: PLANO:; PROYECTO:; NOMBRE: ESCALA:; FECHA: No:; Pia Pinedo

Vistas Porta Lapiz

http://github.com/PiaPinedo/DrawMakina Porta Lapiz

A (2:1)

6 | 1 | Tornillo M4x16 2 | 43

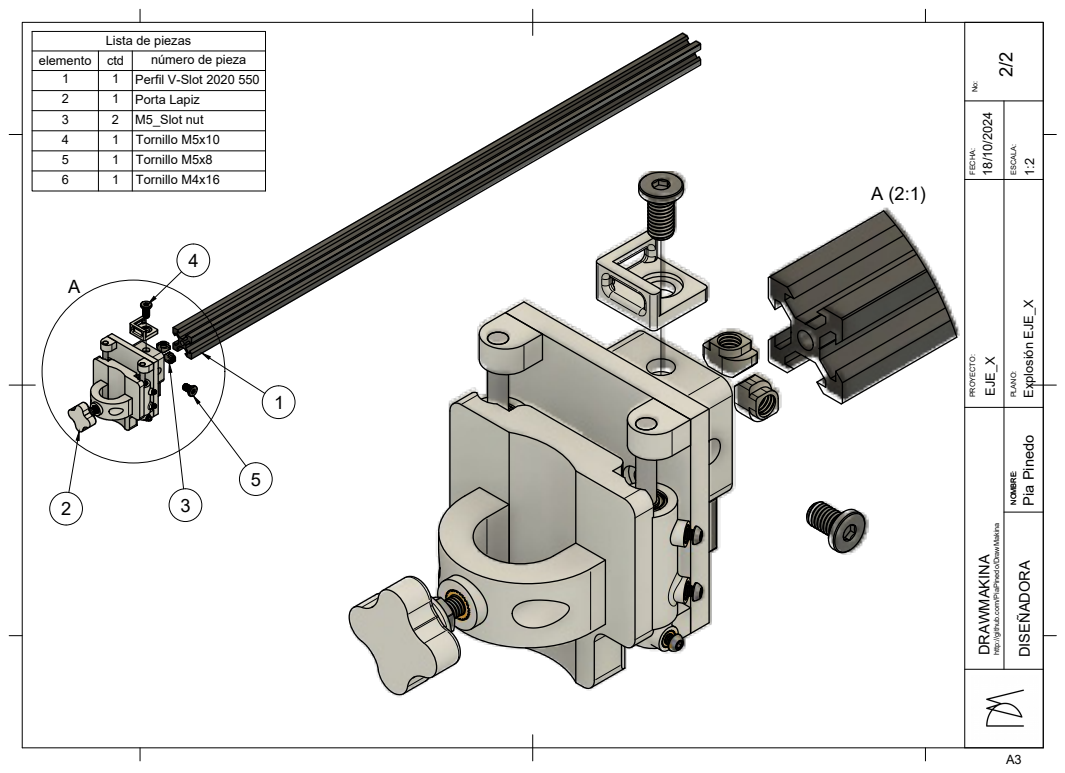
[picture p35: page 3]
DRAWMAKINA; DISEÑADORA; NOMBRE: PLANO:; PROYECTO:; NOMBRE: ESCALA:; FECHA: No:; Pia Pinedo; Explosión EJE_X; elemento; ctd; número de pieza; Perfil V-Slot 2020 550; Porta Lapiz; M5_Slot nut 4; Tornillo M5x10 5; Tornillo M5x8

Lista de piezas

http://github.com/PiaPinedo/DrawMakina EJE_X

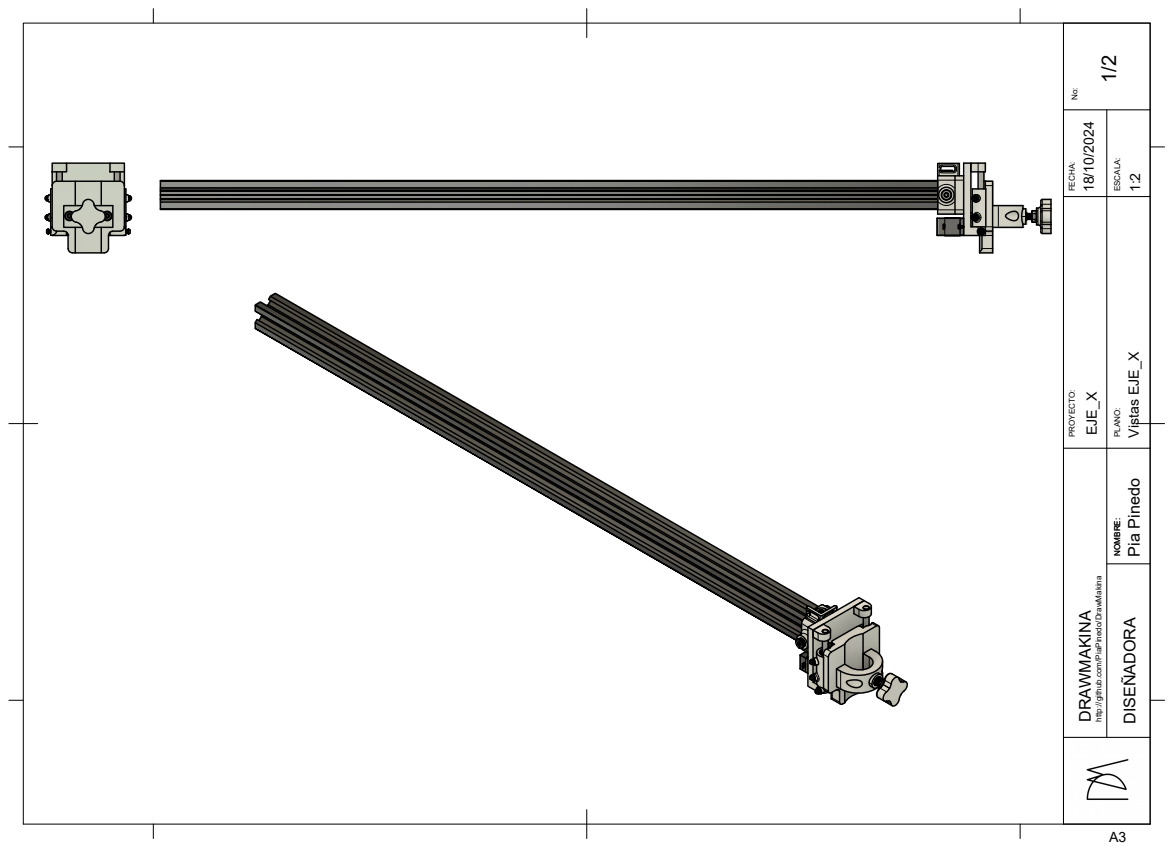
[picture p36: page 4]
DRAWMAKINA; DISEÑADORA; NOMBRE: PLANO:; PROYECTO:; NOMBRE: ESCALA:; FECHA: No:; Pia Pinedo; Vistas EJE_X

http://github.com/PiaPinedo/DrawMakina EJE_X

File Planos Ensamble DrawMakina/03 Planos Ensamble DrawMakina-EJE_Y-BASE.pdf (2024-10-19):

3

1

DRAWMAKINA; DISEÑADORA; NOMBRE: PLANO:; PROYECTO:; NOMBRE: ESCALA:; FECHA: No:; Pia Pinedo; Explosión EJE_Y; element o; ctd; nombre de pieza; Pieza Motor_Y v2; Nema17_34mm v1; Tornillo M3x8 v1; Perfil V-Slot 2040 800 v2 5; Tornillo M5x10 v1; GT2 Timing Pulley 20 Tooth v2

Lista de piezas

http://github.com/PiaPinedo/DrawMakina EJE_Y

DRAWMAKINA; DISEÑADORA; NOMBRE: PLANO:; PROYECTO:; NOMBRE: ESCALA:; FECHA: No:; Pia Pinedo; Vistas EJE_Y

http://github.com/PiaPinedo/DrawMakina EJE_Y

6 | 2 | Tornillo M5x8 3

DRAWMAKINA; DISEÑADORA; NOMBRE: PLANO:; PROYECTO:; NOMBRE: ESCALA:; FECHA: No:; Pia Pinedo; elemento; ctd; número de pieza; Perfil V-Slot 2040 250; Tapa 20x40 3; Tornillo M5x10 4; Angle Bracket 2020 5; M5_Slot nut

Lista de piezas

http://github.com/PiaPinedo/DrawMakina BASE Slot 2040x300 18/10/2024

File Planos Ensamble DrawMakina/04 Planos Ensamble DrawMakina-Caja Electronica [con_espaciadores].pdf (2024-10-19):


DRAWMAKINA DISEÑADORA NOMBRE: PROYECTO: PLANO: FECHA: ESCALA: No: Pia Pinedo http://github.com/PiaPinedo/DrawMakina Caja Electronica [con_espaciadores] Vistas Caja Electronica 19/10/2024 1:1 1/2

elemento; ctd; número de pieza 1; BASE DM 2; TRASERA op 24V 3; LATERAL_A op rejilla 4; FRONTAL DM 5; LATERAL_B 6; Espaciador male-female M3x6 5

Lista de piezas

DRAWMAKINA DISEÑADORA NOMBRE: PROYECTO: PLANO: FECHA: ESCALA: No: Pia Pinedo http://github.com/PiaPinedo/DrawMakina Caja Electronica [con_espaciadores] Explosión aja Electronica 19/10/2024 1:1 2/2

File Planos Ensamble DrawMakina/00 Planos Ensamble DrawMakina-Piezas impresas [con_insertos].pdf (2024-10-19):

DRAWMAKINA; DISEÑADORA; NOMBRE:; PROYECTO:; PLANO:; FECHA:; ESCALA:; Pia Pinedo; elemento; ctd; número de pieza; Porta lapiz_1; RUTHEX_M3x5_7; RUTHEX_M4X8_1

Lista de piezas

http://github.com/PiaPinedo/DrawMakina Porta lapiz_1 [con_insertos] 19/10/2024

DRAWMAKINA; DISEÑADORA; NOMBRE:; PROYECTO:; PLANO:; FECHA:; ESCALA:; Pia Pinedo; Vistas Porta lapiz_2; elemento; ctd; número de pieza; Porta lapiz_2; RUTHEX_M2x4

http://github.com/PiaPinedo/DrawMakina Porta lapiz_2 [con_insertos]

DRAWMAKINA; DISEÑADORA; NOMBRE:; PROYECTO:; PLANO:; FECHA:; ESCALA:; Pia Pinedo; elemento; ctd; número de pieza; Porta lapiz_3; RUTHEX_M3x5_7; RUTHEX_M2x4; Linear_bearing_LM4UU; Tornillo M2x6

http://github.com/PiaPinedo/DrawMakina Porta lapiz_3 [con_insertos][con_rodamiento] 19/10/2024

DRAWMAKINA; DISEÑADORA; NOMBRE:; PROYECTO:; PLANO:; FECHA:; ESCALA:; Pia Pinedo; elemento; ctd; número de pieza; Porta lapiz_4; RUTHEX_M4X8_1

http://github.com/PiaPinedo/DrawMakina Porta lapiz_4 [con insertos] 19/10/2024

DRAWMAKINA; DISEÑADORA; NOMBRE:; PROYECTO:; PLANO:; FECHA:; ESCALA:; Pia Pinedo; elemento; ctd; número de pieza; Porta lapiz_Roseta; RUTHEX_M4X8_1; Tornillo prisionero M4x30 4; Tuerca M4

http://github.com/PiaPinedo/DrawMakina Porta lapiz_Roseta [con_inserto] 19/10/2024

DRAWMAKINA; DISEÑADORA; NOMBRE:; PROYECTO:; PLANO:; FECHA:; ESCALA:; Pia Pinedo; elemento; ctd; número de pieza; Pieza Final X; RUTHEX_M4X8_1

http://github.com/PiaPinedo/DrawMakina Final X [con_insertos] 19/10/2024

DRAWMAKINA; DISEÑADORA; NOMBRE:; PROYECTO:; PLANO:; FECHA:; ESCALA:; Pia Pinedo; elemento; ctd; número de pieza; Pieza final carrera; RUTHEX_M2x4

http://github.com/PiaPinedo/DrawMakina Pieza final carrera [con_insertos] 19/10/2024

DRAWMAKINA; DISEÑADORA; NOMBRE:; PROYECTO:; PLANO:; FECHA:; ESCALA:; Pia Pinedo

http://github.com/PiaPinedo/DrawMakina Placa Carro X [con_insertos]

Vistas Placa Carro X

DRAWMAKINA; DISEÑADORA; NOMBRE:; PROYECTO:; PLANO:; FECHA:; ESCALA:; Pia Pinedo; elemento; ctd; número de pieza; Placa Carro X; RUTHEX_M3x5_7; RUTHEX_M2x4

http://github.com/PiaPinedo/DrawMakina Placa Carro X [con_insertos]

Explosión Placa Carro X

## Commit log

2024-10-15 Create STL
    Archivos STL para imprimir 3D
2024-10-15 Add files via upload
    Archivos STL para la impresión 3d
    [Pieza Final X v2.stl, Pieza Motor_Y.stl, Pieza Portacable_1.stl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]
